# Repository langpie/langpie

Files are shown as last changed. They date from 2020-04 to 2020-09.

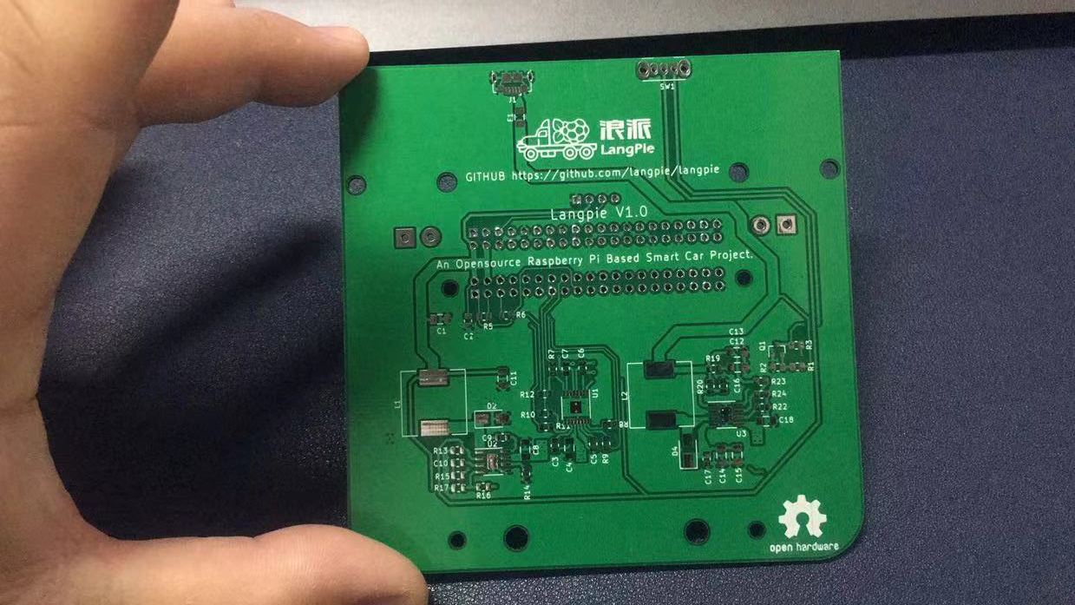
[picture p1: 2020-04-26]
documents/images/real_pcb_v1_0.jpg

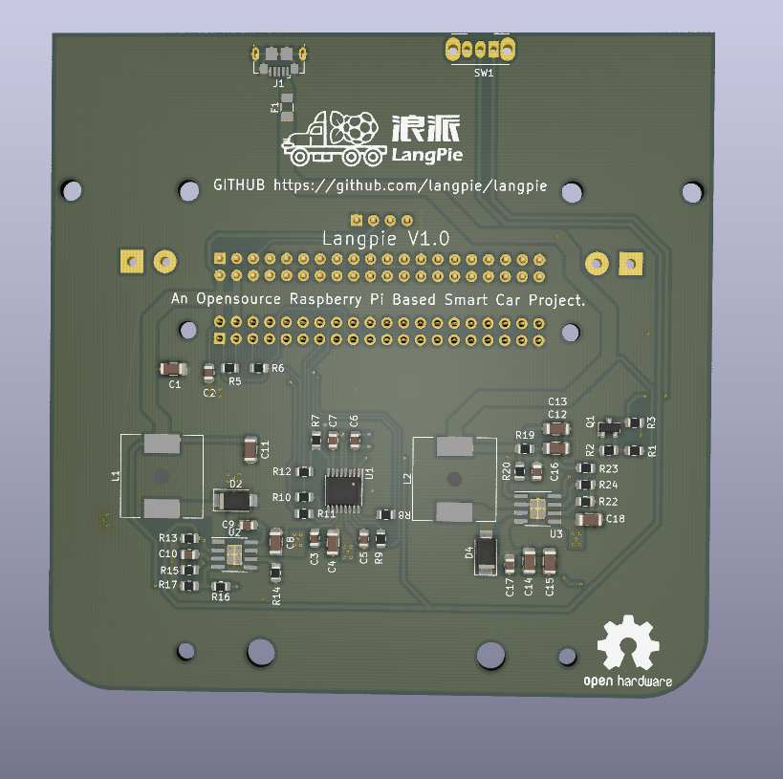
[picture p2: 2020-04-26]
documents/images/pcb_v1_2.png

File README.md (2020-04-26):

# langpie 项目

# 树莓派分布式自动驾驶小车项目-浪派项目
## Respberry Pi LangPie Open Source Project

## 项目目标
* V1.0 阶段: 让树莓派小车能够跑起来(浪)
* V2.0 阶段: 让树莓派能够狠狠的浪(例如加入机器视觉)
* V3.0 阶段: 让树莓派能够狂浪(能够浪到指定地点)
* V4.0 阶段: 让每个人的树莓派能够一起浪(浪派对)
* V5.0 阶段: 让树莓派能够用神经网络自己判断自己该去哪里浪(放浪形骸)
* V6.0 阶段: 树莓派贾维斯浪催的小犊子(没谱)

## 目前状态
### V1.0 版本
- [ ] 电路图绘制
- [ ] 机械图绘制
- [ ] 电路图 Layout
- [ ] 电路板打板
- [ ] 购买元器件
- [ ] 设备焊接
- [ ] 小车组装
- [ ] 树莓派系统安装
- [ ] wiringPi 安装调试
- [ ] 测试电源
- [ ] 测试充电
- [ ] 测试马达
- [ ] 测试树莓派驱动
- [ ] 测试 OLED 屏幕
- [ ] 测试LED 灯
 
## 项目组成员 including Email：

* 圈圈  bg3mdo#langpie.ga
* 漂移菌  yoyojack#langpie.ga
* DoubleDog  doubledog#langpie.ga
* hahaha  hahaha#langpie.ga
* 刘津屹  liujinyi#langpie.ga
* 中华绘图铅笔  pencil#langpie.ga
* 飞鸿  bg3nit#langpie.ga
* 洋洋大叔  bi3qdn#langpie.ga
* 祁建鑫  qjx#langpie.ga
* wjcwqc  wjcwqc#langpie.ga
* 小白 dmuxiaobai#langpie.ga
* lqh  lqh#langpie.ga
* kwanghue kwanghue#langpie.ga
* 张翼 zy#langpie.ga
* iChizer0 

##  项目站点 Project website: 

www.langpie.ga

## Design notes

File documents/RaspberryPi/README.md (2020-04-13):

# Raspberry Pi 树莓派软件准备

## 操作系统镜像

* 强烈推荐: raspbian 
```bash
Distributor ID:	Raspbian
Description:	Raspbian GNU/Linux 10 (buster)
Release:	10
Codename:	buster
```
* 镜像连接: www.raspberrypi.org/downloads/

## 烧录工具

* Etcher: etcher.io
* Win32_diskimager: 请自行百度

## 远程登录工具

* Putty
* Xshell
* SecureCRT
* Rshell
* Powershell

## 文件传输工具

* Windows: 推荐 filezilla / sftp 
* Mac: scp
* Linux: scp

## 自动更换源脚本使用方法
```bash
git clone https://github.com/langpie/langpie.git
cd langpie/documents/RaspberryPi/
chmod +x auto_tsinghua_source.sh
./auto_tsinghua_source.sh
```
### Have Fun

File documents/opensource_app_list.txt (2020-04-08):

# Raspberry Pi Based Open Source Smart Car
# Open Source Design Software

## PCB Design Kit
    -KiCAD
    https://www.kicad-pcb.org/

## Mechanical Design Kit
    -FreeCAD
    https://www.freecadweb.org/

## Image Editor
    -GIMP
    https://www.gimp.org/

## Vector Graphic Editor
    -InkScape
    https://inkscape.org/

## Visio Alternatives
    -Pencil Project
    https://pencil.evolus.vn/

## Office Alternatives
    -LibreOffice
    https://www.libreoffice.org/
    -OpenOffice
    https://www.openoffice.org/
    -WPS
    https://www.wps.com/

## Mind Map
    -XMind
    https://www.xmind.net/

## Project Management
    -GanttProject
    https://www.ganttproject.biz/

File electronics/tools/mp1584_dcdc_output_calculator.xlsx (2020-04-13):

Output(V) | R1(Kilo Ohm) | R2 (Kilo Ohm, Less than 40K) | FB(V)
5.212121212 | 182 | 33 | 0.8
Note that it is better to use E3/E6/E12/E24/E96 standard resistor values

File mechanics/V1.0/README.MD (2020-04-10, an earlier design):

2020.4.10 优化了电机座 完善了摄像头支架 创建了3D打印所需的STL文件

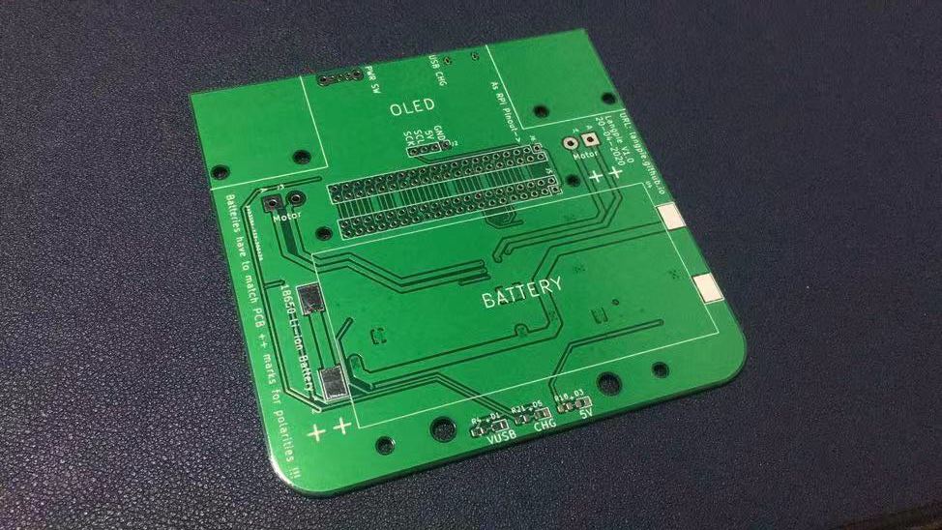
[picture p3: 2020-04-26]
documents/images/real_pcb_v1_1.jpg.jpg

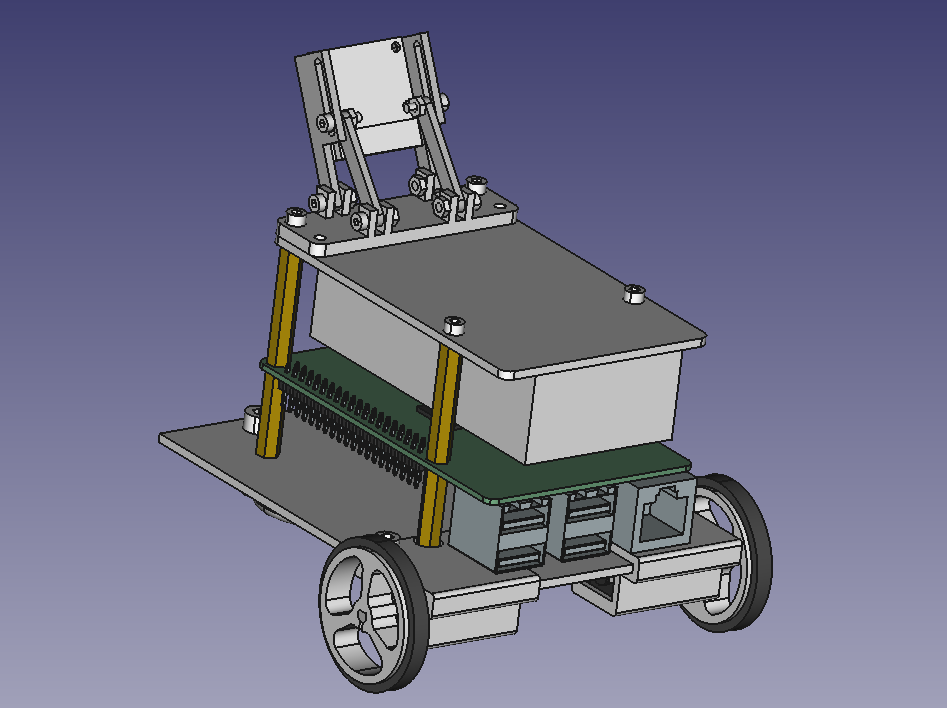
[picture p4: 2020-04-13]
documents/images/cad_v1_1.png

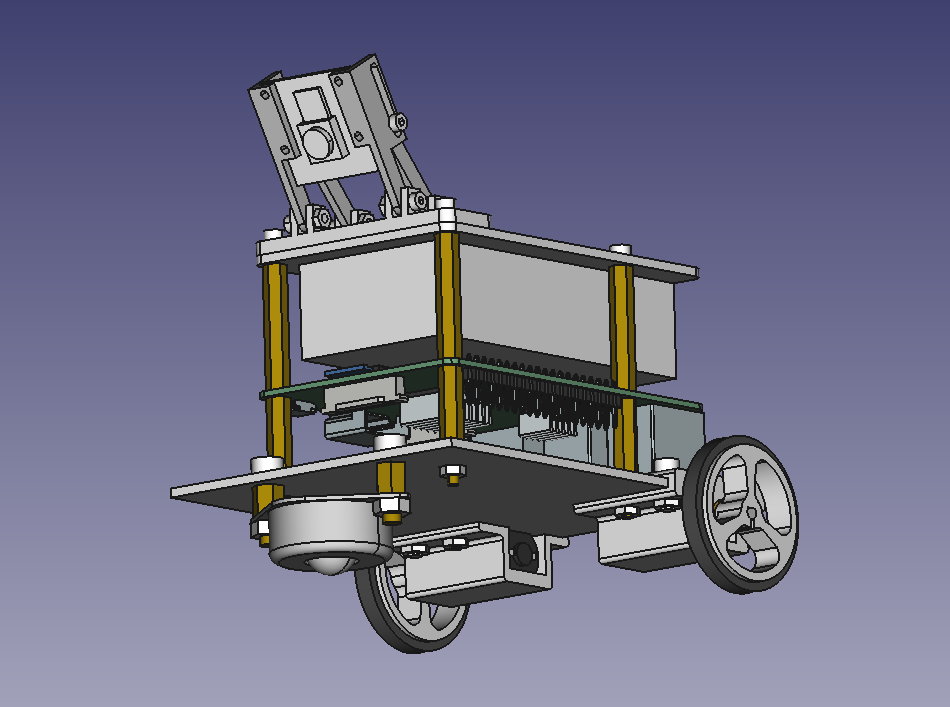
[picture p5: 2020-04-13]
documents/images/cad_v1_0.png

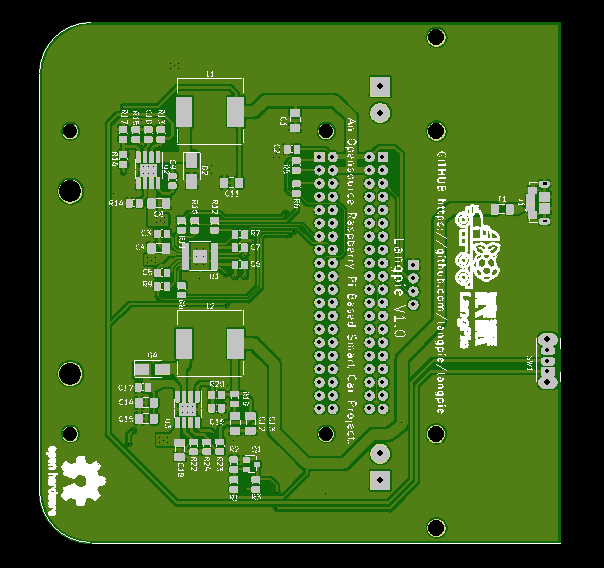
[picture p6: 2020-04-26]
documents/images/fab_v1_preview_0.png

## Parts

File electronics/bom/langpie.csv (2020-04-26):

Id | Designator | Package | Quantity | Designation | Supplier and ref
1 | G*** | logo | 1 | LOGO
2 | REF** | OSHW-Logo2_14.6x12mm_SilkScreen | 1 | OSHW-Logo2_14.6x12mm_SilkScreen
3 | ,,,,, |  | 6
4 | C5 | C_0805_2012Metric | 1 | 2.2uF
5 | R15,R14,R24 | R_0805_2012Metric | 3 | 100K
6 | J6 | PinHeader_2x20_P2.54mm_Vertical | 1 | Conn_02x20_Odd_Even
7 | , , , | MountingHole_2.7mm_M2.5 | 4 | MountingHole_2.7mm_M2.5
8 | , | MountingHole_4.3mm_M4 | 2 | MountingHole_4.3mm_M4
9 | , , , | MountingHole_3.2mm_M3 | 4 | MountingHole_3.2mm_M3
10 | C1 | C_1206_3216Metric | 1 | 10nF
11 | C2,C6,C7,C9 | C_0805_2012Metric | 4 | 100nF
12 | C3 | C_0805_2012Metric | 1 | 10nF
13 | C4,C8,C12,C18 | C_1206_3216Metric | 4 | 10uF
14 | C10 | C_0805_2012Metric | 1 | 150pF
15 | C11,C13,C14,C15 | C_1206_3216Metric | 4 | 22uF
16 | C16,C17 | C_0805_2012Metric | 2 | 1uF
17 | D1,D3,D5 | LED_0805_2012Metric | 3 | LED
18 | D2,D4 | D_SMA | 2 | B340A-13-F
19 | F1 | Fuse_1206_3216Metric | 1 | Fuse
20 | J1 | USB_Micro-B_GCT_USB3076-30-A | 1 | USB_B_Micro
21 | J2 | PinHeader_1x04_P2.54mm_Vertical | 1 | Conn_01x04
22 | J3,J4 | SolderWirePad_1x02_P5.08mm_Drill1.5mm | 2 | Conn_01x02
23 | J5 | PinSocket_2x20_P2.54mm_Vertical | 1 | Conn_02x20_Odd_Even
24 | L1 | L_12x12mm_H6mm | 1 | 15uH
25 | L2 | L_12x12mm_H6mm | 1 | 2.2uH
26 | Q1 | SOT-23 | 1 | 2N7000
27 | R1,R4,R18 | R_0805_2012Metric | 3 | 1K
28 | R2,R13 | R_0805_2012Metric | 2 | 47K
29 | R3,R5,R6,R12 | R_0805_2012Metric | 4 | 10K
30 | R7,R8,R9,R10,R11,R21 | R_0805_2012Metric | 6 | 200R
31 | R16 | R_0805_2012Metric | 1 | 182K
32 | R17 | R_0805_2012Metric | 1 | 33K
33 | R19,R20 | R_0805_2012Metric | 2 | 2R
34 | R22 | R_0805_2012Metric | 1 | 6.8K
35 | R23 | R_0805_2012Metric | 1 | 270K
36 | SW1 | SW_CuK_OS102011MA1QN1_SPDT_Angled | 1 | SW_SPDT
37 | U1 | HTSSOP-16-1EP_4.4x5mm_P0.65mm_EP3.4x5mm_Mask2.46x2.31mm_ThermalVias | 1 | DRV8833PWP
38 | U3 | SOIC-8-1EP_3.9x4.9mm_P1.27mm_EP2.29x3mm_ThermalVias | 1 | CS5080E
39 | U4 | li-battery-case | 1 | 18650-Battery
40 | U2 | SOIC-8-1EP_3.9x4.9mm_P1.27mm_EP2.29x3mm_ThermalVias | 1 | MP1584

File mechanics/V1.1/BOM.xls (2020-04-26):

项目号 | 零件号 | 说明 | 数量 | 型号 | 淘宝链接
1 | N20 wheel |  | 2
2 | M2.5 28+6 |  | 6
3 | M2.5 nut |  | 4
4 | M3 8 hexagon socket head cap screw |  | 4
5 | M3 nut |  | 4
6 | N20 motor |  | 2
7 | M4 6 hexagon socket head cap screw |  | 2
8 | ball wheel |  | 1 | 12A | https://detail.tmall.com/item.htm?spm=a230r.1.14.28.3d3b42fdA0ATDi&id=590284019863&ns=1&abbucket=13
9 | M4 7+6 copper cylinder |  | 2
10 | M4 nut |  | 2
11 | battery holder |  | 1
12 | M2 6 hexagon socket head cap screw |  | 2
13 | M2 nut |  | 6
14 | M2 8 hexagon socket head cap screw |  | 4

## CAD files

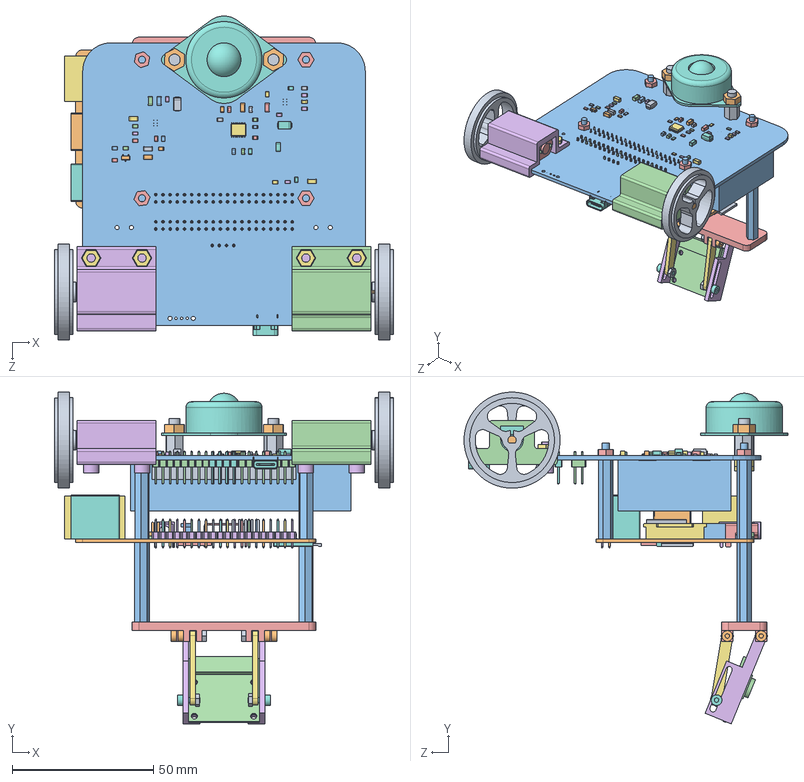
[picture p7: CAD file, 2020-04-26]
mechanics/V1.1/car.SLDASM
120.0 x 117.4 x 114.6 mm
N20 wheel x 2
Raspberry Pi 3_1.stp
Raspberry Pi 3_1_1.stp
Raspberry Pi 3_2.stp
Raspberry Pi 3_3.stp
Raspberry Pi 3_4.stp
Raspberry Pi 3_5.stp
Raspberry Pi 3_6.stp
Raspberry Pi 3_7.stp
Raspberry Pi 3_8.stp
Raspberry Pi 3_9.stp
Raspberry Pi 3_10.stp
Raspberry Pi 3_11.stp
Raspberry Pi 3_12.stp
Raspberry Pi 3_13.stp
Raspberry Pi 3_14.stp
Raspberry Pi 3_15.stp
Raspberry Pi 3_16.stp
Raspberry Pi 3_17.stp
Raspberry Pi 3_18.stp
Raspberry Pi 3_19.stp
Raspberry Pi 3_20.stp
Raspberry Pi 3_21.stp
Raspberry Pi 3_22.stp
Raspberry Pi 3_23.stp
Raspberry Pi 3_24.stp
Raspberry Pi 3_25.stp
Raspberry Pi 3_26.stp
Raspberry Pi 3_27.stp
Raspberry Pi 3_28.stp
Raspberry Pi 3_29.stp
Raspberry Pi 3_30.stp
Raspberry Pi 3_31.stp
Raspberry Pi 3_32.stp
Raspberry Pi 3_33.stp
Raspberry Pi 3_34.stp
Raspberry Pi 3_35.stp
Raspberry Pi 3_36.stp
Raspberry Pi 3_37.stp
Raspberry Pi 3_38.stp
Raspberry Pi 3_39.stp
Raspberry Pi 3_40.stp
Raspberry Pi 3_41.stp
Raspberry Pi 3_42.stp
Raspberry Pi 3_43.stp
Raspberry Pi 3_44.stp
Raspberry Pi 3_45.stp
Raspberry Pi 3_46.stp
Raspberry Pi 3 (micro SD).stp
Raspberry Pi 3_47.stp
Raspberry Pi 3_48.stp
Raspberry Pi 3_49.stp
Raspberry Pi 3_50.stp
Raspberry Pi 3_51.stp
Raspberry Pi 3_52.stp
Raspberry Pi 3_53.stp
RPi Heatsink Set.stp
RPi Heatsink Set_1.stp
M2.5 28+6 x 6
N20 lift mounting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

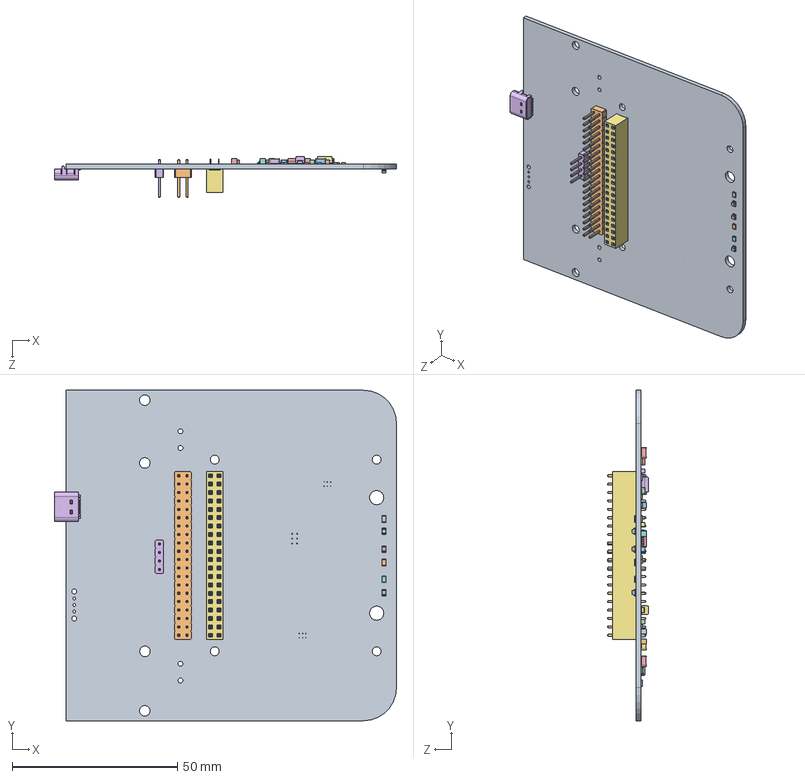
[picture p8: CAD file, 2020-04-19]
mechanics/V1.1/CAR PCB/car pcb.SLDASM
103.5 x 100.0 x 12.4 mm
J6_PinHeader_2x20_P254mm_Vertical_5E973953
D1_LED_0805_2012Metric_5E97381B
D3_LED_0805_2012Metric_5E973846
D5_LED_0805_2012Metric_5E973871
J2_PinHeader_1x04_P254mm_Vertical_5E9738C1
J5_PinSocket_2x20_P254mm_Vertical_5E975A58
R4_R_0805_2012Metric_5E99E94D
R18_R_0805_2012Metric_5E9C048F
R21_R_0805_2012Metric_5E973B6B
C5_C_0805_2012Metric_5E97372B
R15_R_0805_2012Metric_5E973B05
C1_C_1206_3216Metric_5E9736E7
C2_C_0805_2012Metric_5E9736F8
C3_C_0805_2012Metric_5E973709
C4_C_1206_3216Metric_5E97BBAC
C6_C_0805_2012Metric_5E97B6B1
C7_C_0805_2012Metric_5E97374D
C8_C_1206_3216Metric_5E97375E
C9_C_0805_2012Metric_5E97376F
C10_C_0805_2012Metric_5E973780
C11_C_1206_3216Metric_5E973791
C12_C_1206_3216Metric_5E977737
C13_C_1206_3216Metric_5E978263
C14_C_1206_3216Metric_5E9737C4
C15_C_1206_3216Metric_5E9737D5
C16_C_0805_2012Metric_5E9737E6
C17_C_0805_2012Metric_5E9737F7
C18_C_1206_3216Metric_5E973808
D2_D_SMA_5E9BCED4
D4_D_SMA_5E9777E8
Q1_SOT_23_5E99EF72
R1_R_0805_2012Metric_5E973A17
R2_R_0805_2012Metric_5E973A28
R3_R_0805_2012Metric_5E973A39
R5_R_0805_2012Metric_5E973A5B
R6_R_0805_2012Metric_5E973A6C
R7_R_0805_2012Metric_5E973A7D
R8_R_0805_2012Metric_5E973A8E
R9_R_0805_2012Metric_5E97BAD9
R10_R_0805_2012Metric_5E973AB0
R11_R_0805_2012Metric_5E973AC1
R12_R_0805_2012Metric_5E97B756
R13_R_0805_2012Metric_5E973AE3
R14_R_0805_2012Metric_5E973AF4
R16_R_0805_2012Metric_5E973B16
R17_R_0805_2012Metric_5E973B27
R19_R_0805_2012Metric_5E973B49
R20_R_0805_2012Metric_5E973B5A
R22_R_0805_2012Metric_5E973B7C
R23_R_0805_2012Metric_5E9785CC
R24_R_0805_2012Metric_5E973B9E
U1_TSSOP_16_1EP_44x5mm_Pitch065mm_EP34x5mm_5E973BE1
User Library-USB Type C Port (SMD Type)

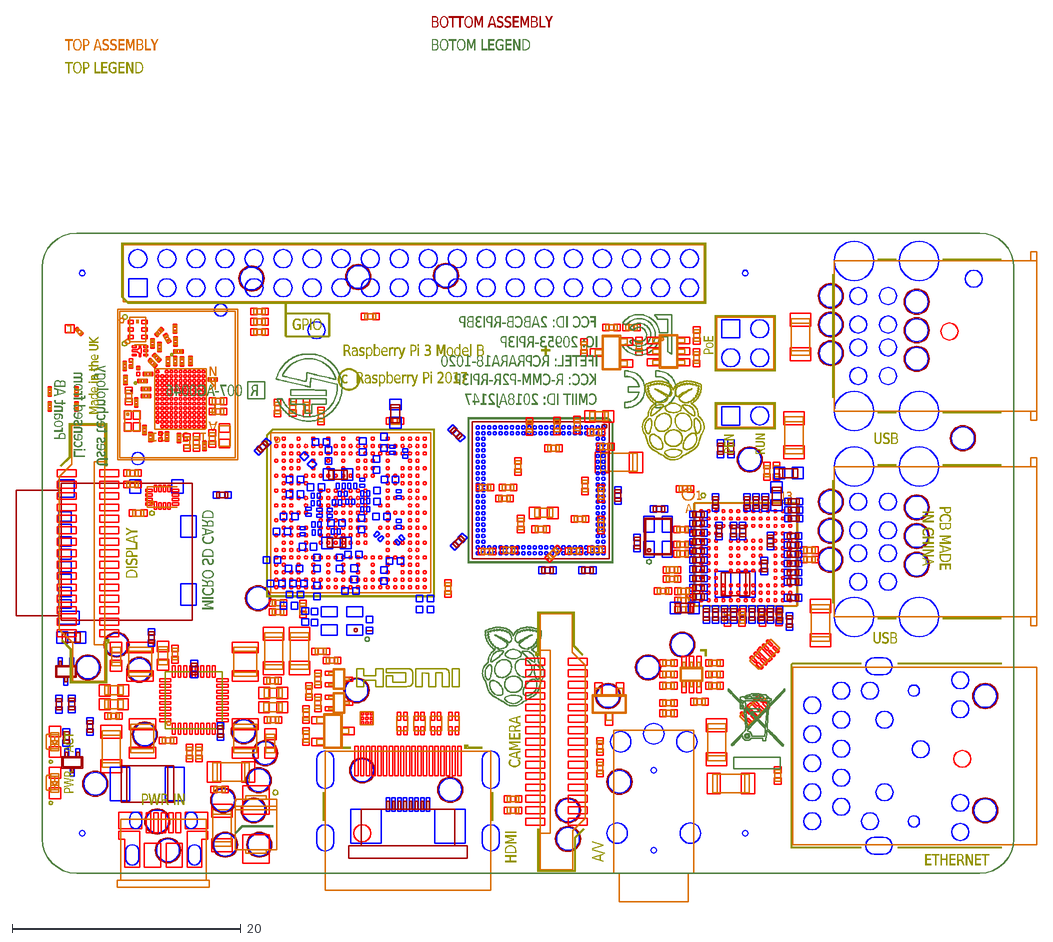
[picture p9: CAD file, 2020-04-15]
electronics/dxf/rpi_MECH_3bplus.dxf
11
5
1
N
K
E
A
13
R 007-AG0046
CMIIT ID: 2018AJ2147
KCC: R-CMM-P2R-RPI3P
IFETEL: RCPRARA18-1020
IN CHINA
PCB MADE
PEN
IC: 20953-RPI3P
FCC ID: 2ABCB-RPI3BP
Licensed from
Proant AB
Uses technology
PoE
c Raspberry Pi 2017
Raspberry Pi 3 Model B
MICRO SD CARD
HDMI
BOTOM LEGEND
BOTTOM ASSEMBLY
TOP LEGEND
TOP ASSEMBLY
Made in the UK
A/V
GPIO
USB
ETHERNET
PWR IN
DISPLAY
CAMERA
RUN
ACT
PWR

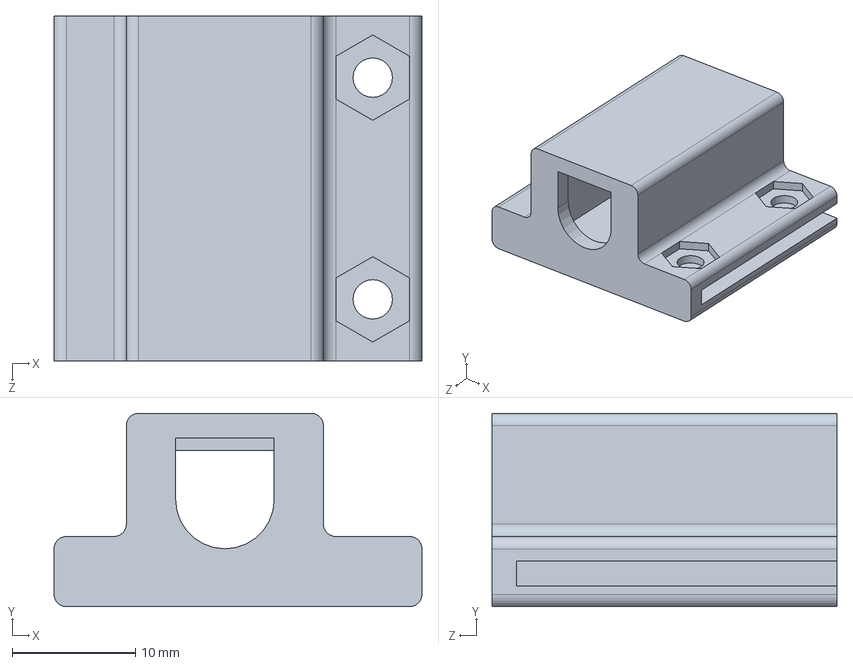
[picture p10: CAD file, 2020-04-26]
mechanics/V1.1/N20 lift mounting.sldprt
29.9 x 15.7 x 28.0 mm

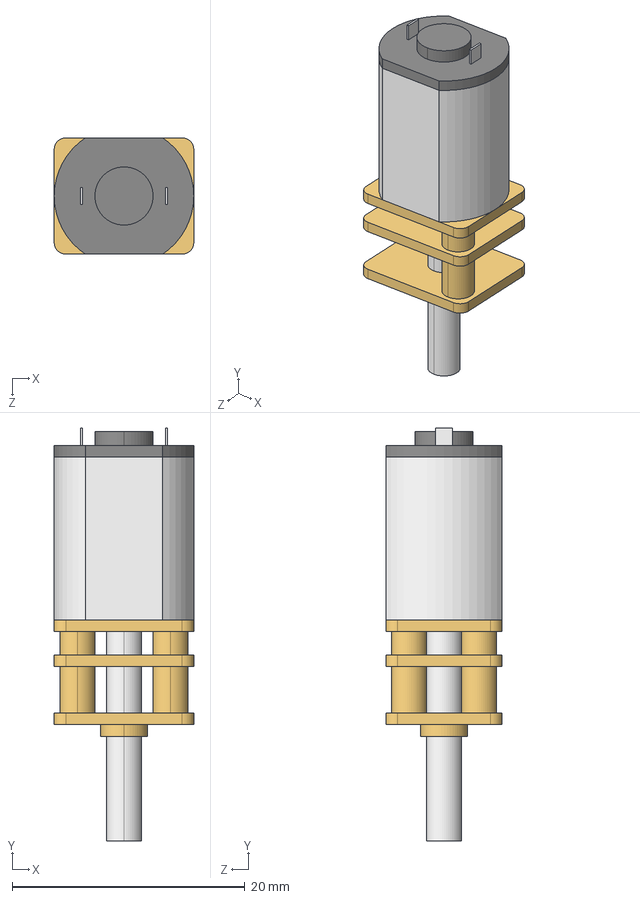
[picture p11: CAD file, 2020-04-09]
mechanics/V1.1/N20motor/User Library-N20.STEP
12.0 x 35.5 x 10.0 mm
User Library-N20_Pad010
User Library-N20_Pad009
User Library-N20_Pad008
User Library-N20_Pad006
User Library-N20_Pad004
User Library-N20_Pad003

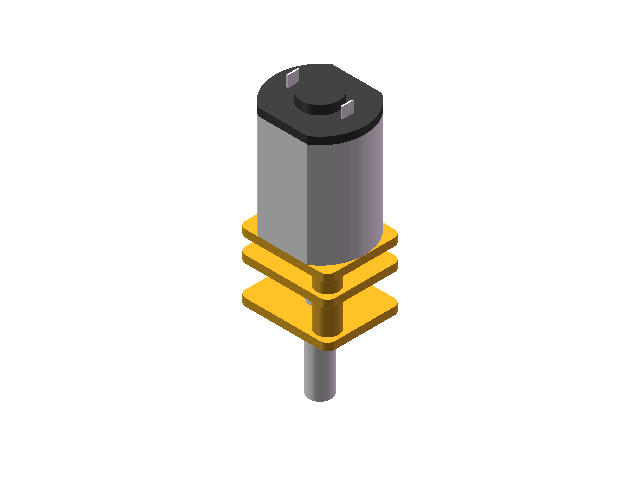
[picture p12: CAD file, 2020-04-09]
mechanics/V1.1/N20motor/N20 motor.SLDASM
User Library-N20_Pad010^User Library-N20(2)
User Library-N20_Pad009^User Library-N20(2)
User Library-N20_Pad008
User Library-N20_Pad006^User Library-N20(2)
User Library-N20_Pad004^User Library-N20(2)
User Library-N20_Pad003^User Library-N20(2)

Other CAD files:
mechanics/V1.1/N20motor/User Library-N20(2).sldasm
mechanics/V1.1/12864oled/Pins.sldasm
mechanics/V1.1/CAR PCB/Top.sldasm
mechanics/V1.1/12864oled/PinHeader.sldasm
mechanics/V1.1/Raspberry/Raspberry Pi 3.stp.SLDASM
mechanics/V1.1/CAR PCB/Step_Models.sldasm
mechanics/V1.1/CAR PCB/Board_Geoms.sldasm
mechanics/V1.1/CAR PCB/Bot.sldasm
mechanics/V1.1/CAR PCB/Pcb.sldasm
mechanics/V1.1/12864oled/128x64Oled v3.sldprt
mechanics/V1.1/CAR PCB/D2_D_SMA_5E9BCED4.sldprt
mechanics/V1.1/Raspberry/Raspberry Pi 3_4.stp.SLDPRT
mechanics/V1.0/DXF/battery pcb.DXF
mechanics/V1.0/DXF/car baseplate.DXF
mechanics/V1.0/M2 nut.SLDPRT
mechanics/V1.0/M2.5 20+6.SLDPRT
mechanics/V1.0/M2.5 28+6.SLDPRT
mechanics/V1.0/M2.5 8 hexagon socket head cap screw.SLDPRT
mechanics/V1.0/M2.5 nut.SLDPRT
mechanics/V1.0/M3 8 hexagon socket head cap screw.SLDPRT
mechanics/V1.0/M3 nut.SLDPRT
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

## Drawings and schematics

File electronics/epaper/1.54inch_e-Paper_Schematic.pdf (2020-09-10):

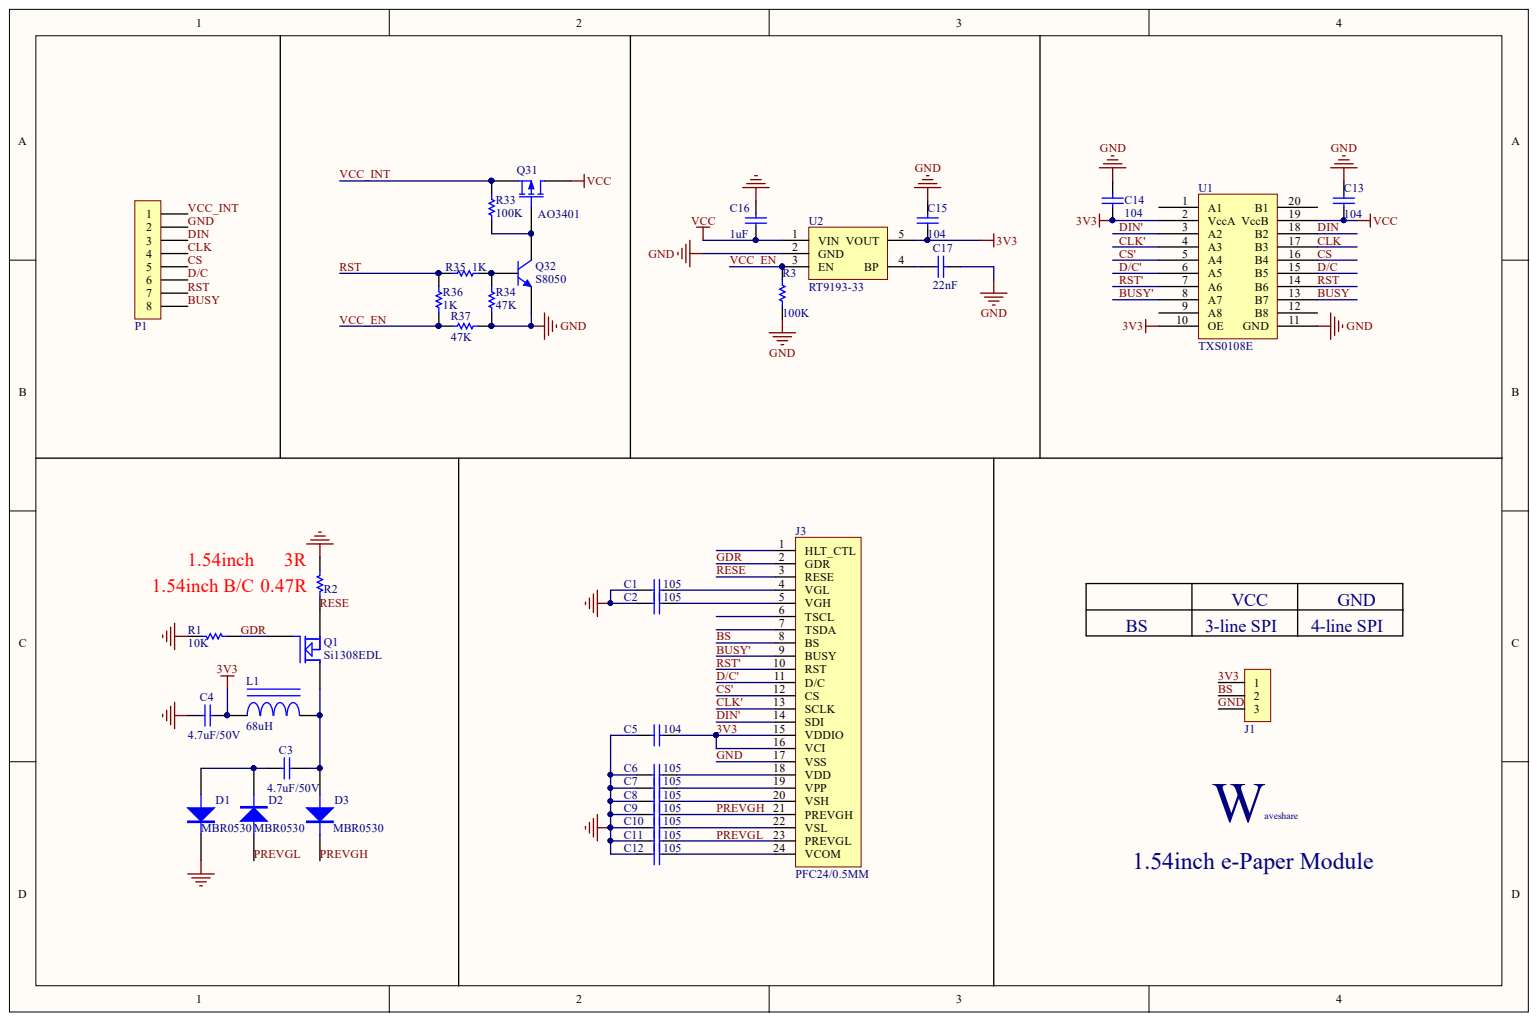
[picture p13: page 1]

VCC | GND

BS | 3-line SPI | 4-line SPI

C7 | 105
C8 | 105
C9 | 105 PREVGH
C10 | 105
C11 | 105 PREVGL
C12 | 105

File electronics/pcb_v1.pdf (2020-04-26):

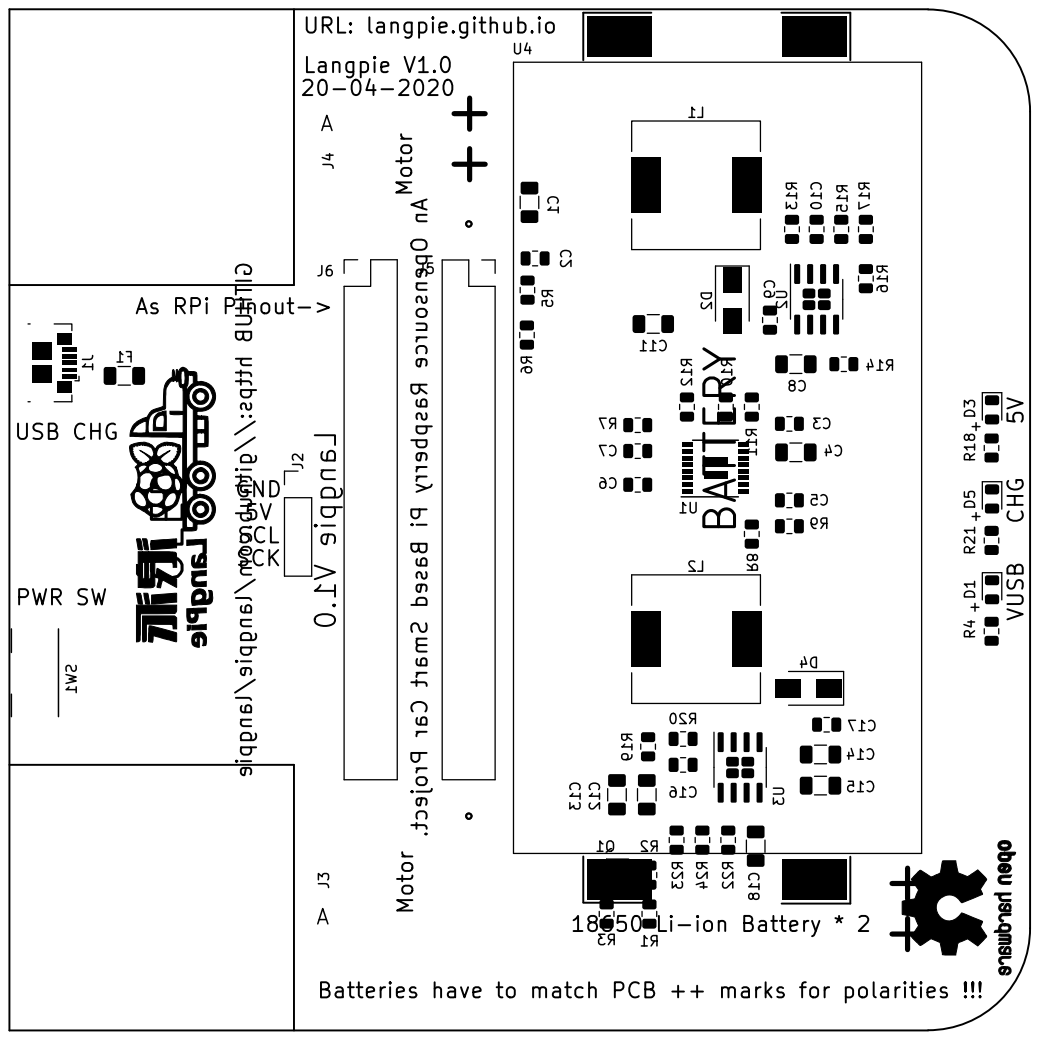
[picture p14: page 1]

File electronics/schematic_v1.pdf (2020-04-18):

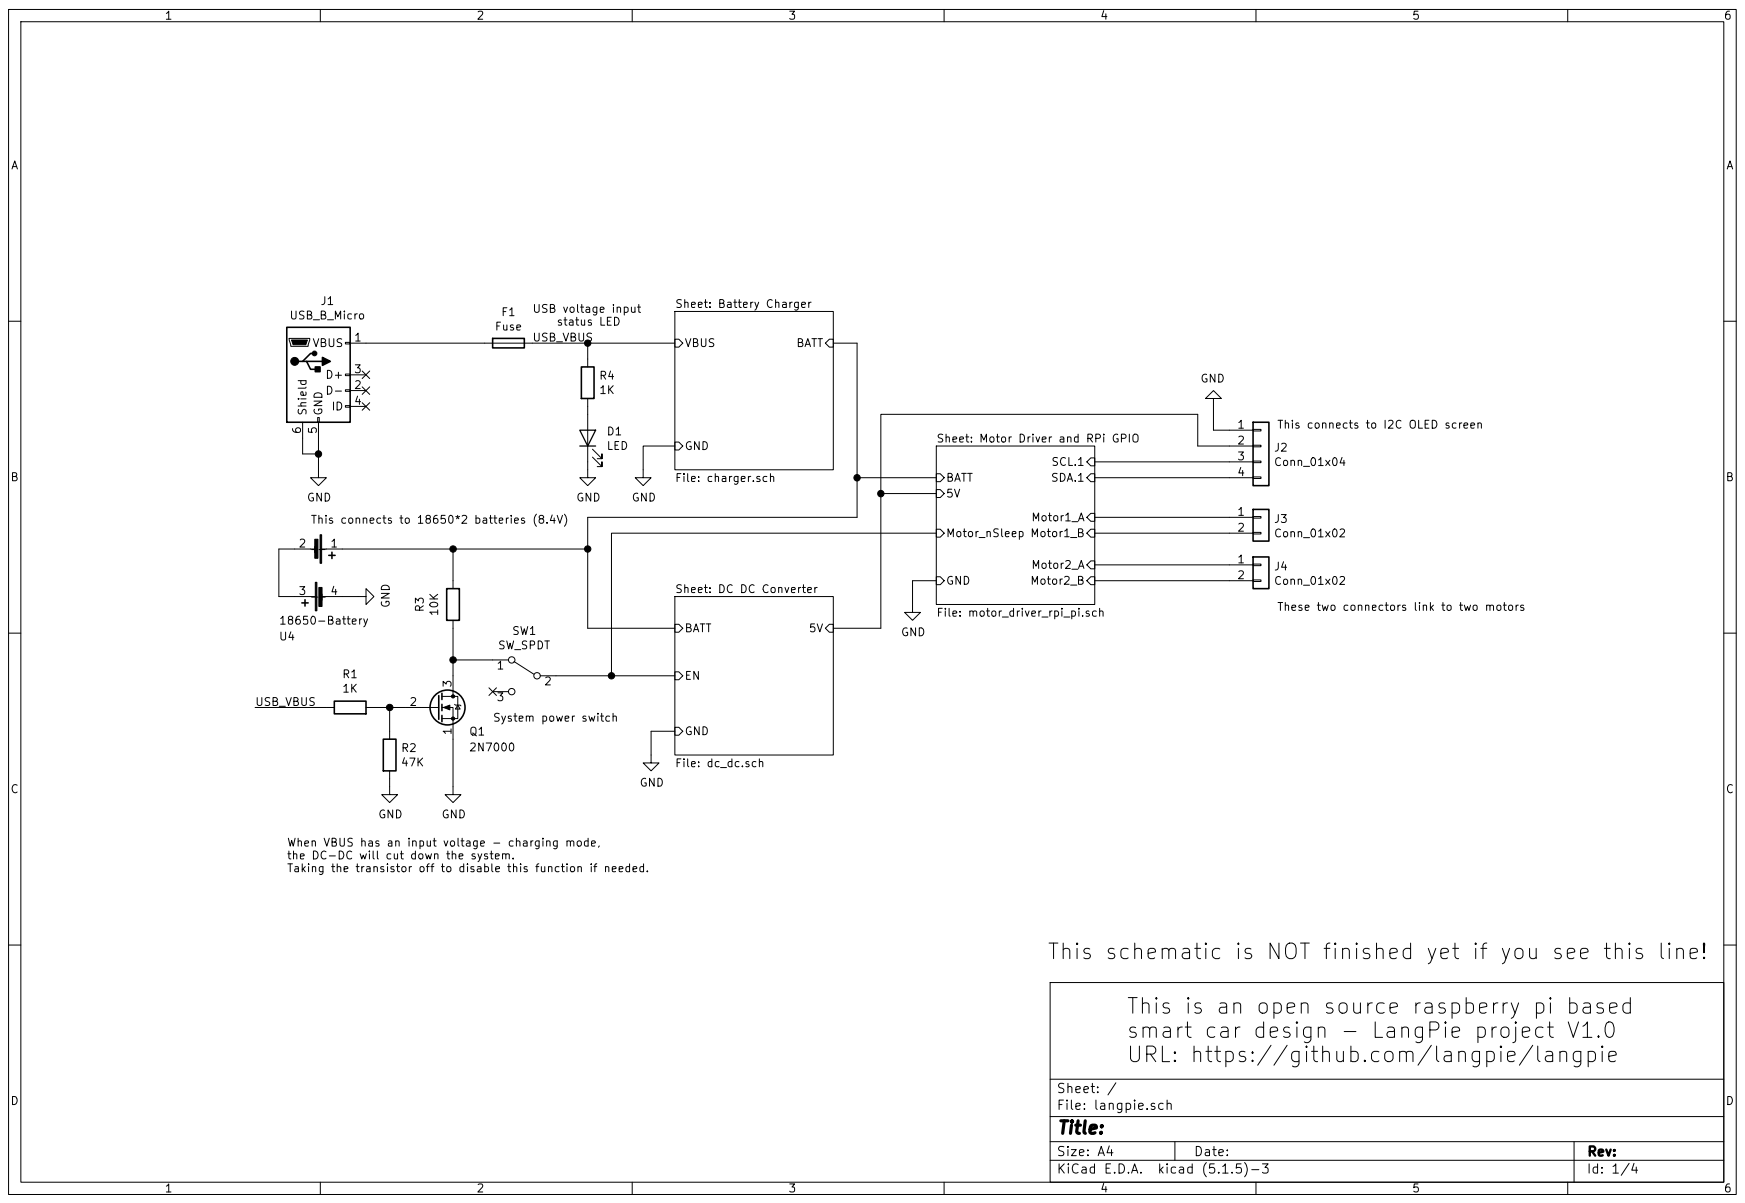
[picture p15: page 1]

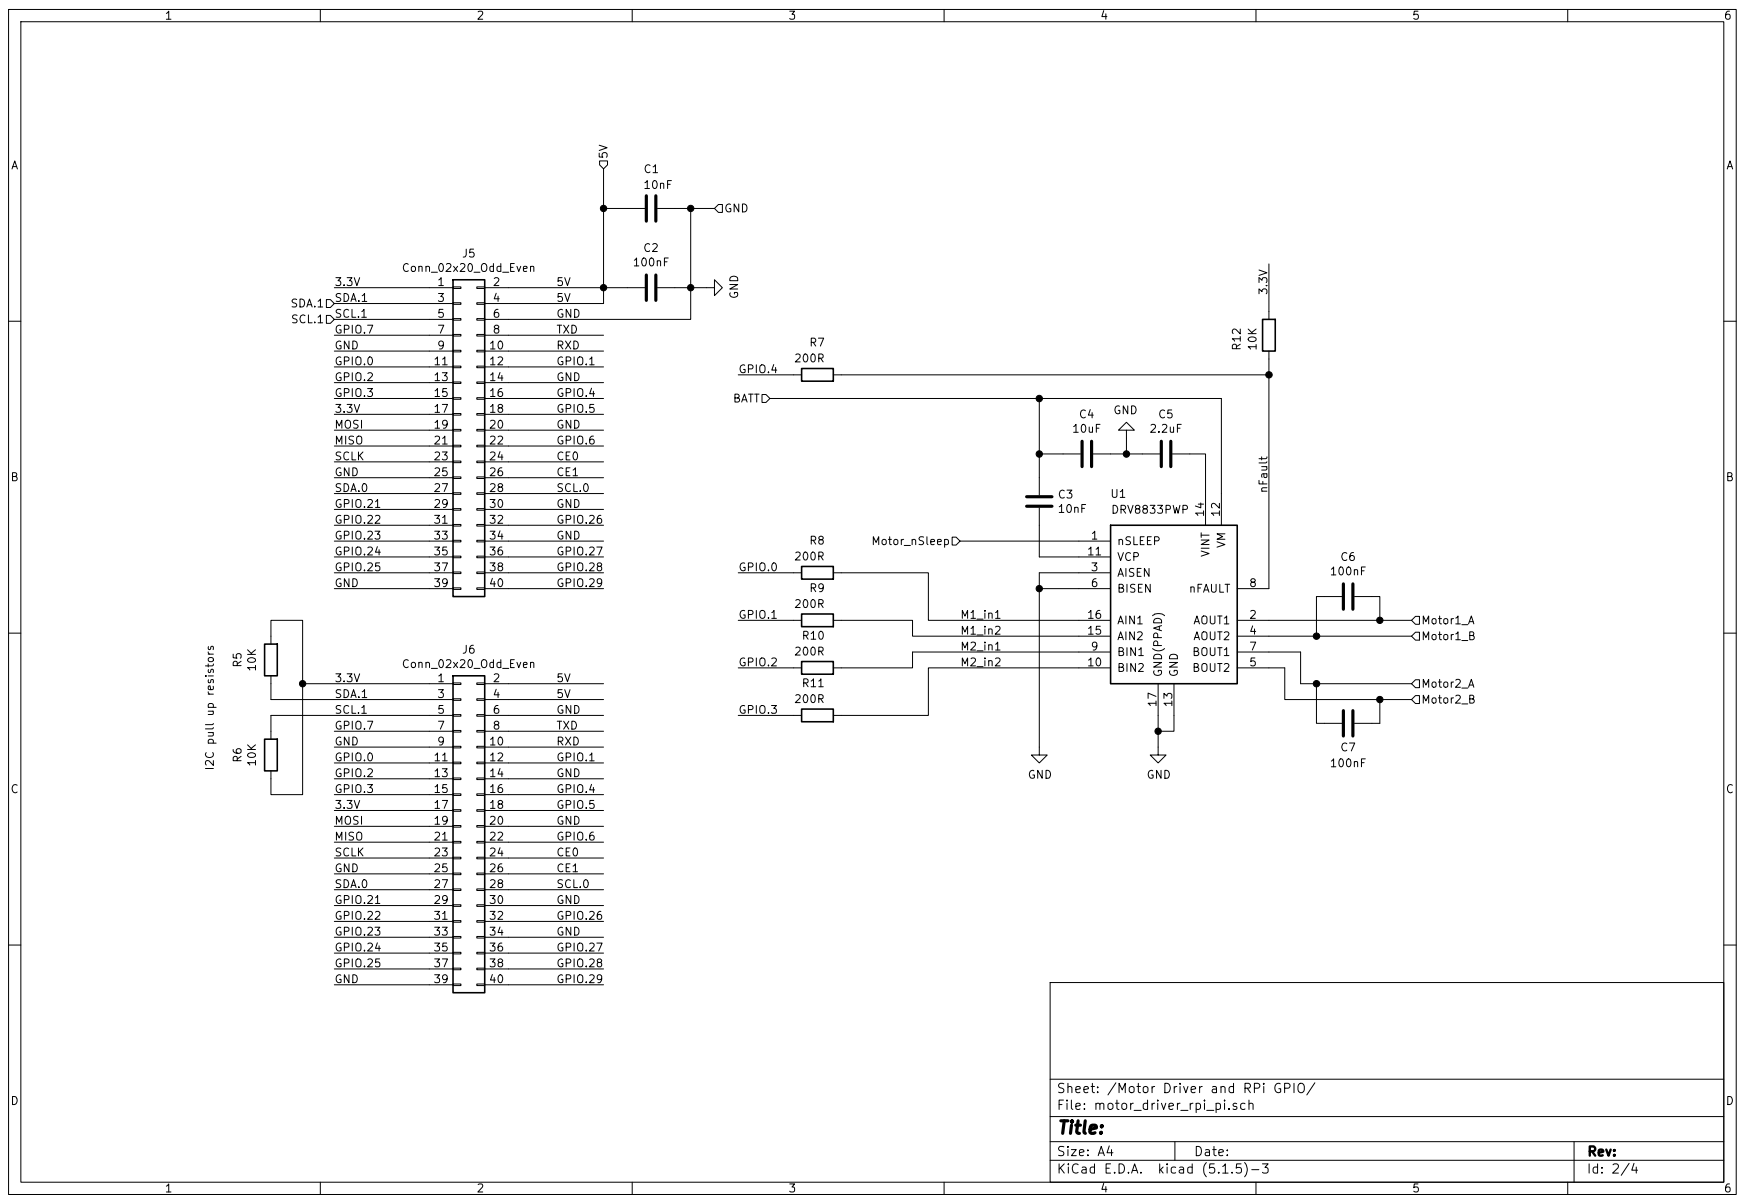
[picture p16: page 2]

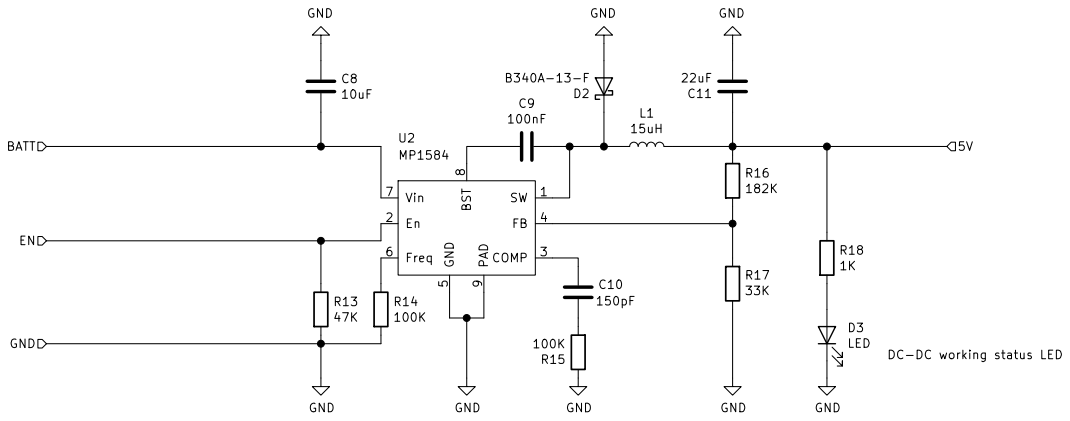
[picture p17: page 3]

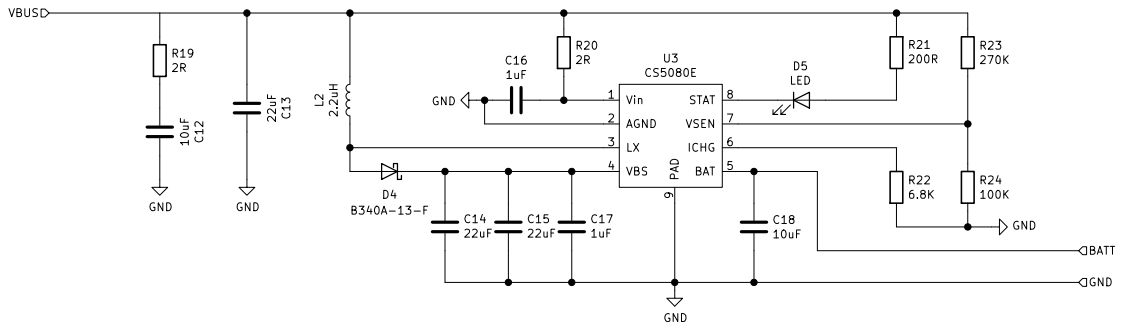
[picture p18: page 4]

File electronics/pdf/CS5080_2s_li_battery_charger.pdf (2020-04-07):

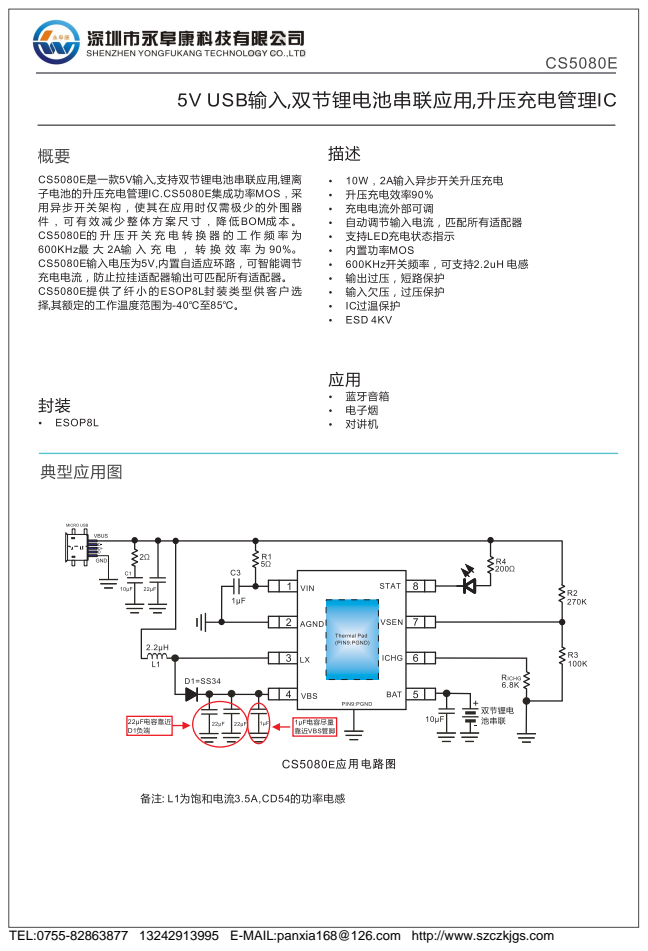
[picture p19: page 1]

TEL:0755-82863877 13242913995 E-MAIL:panxia168@126.com http://www.szczkjgs.com

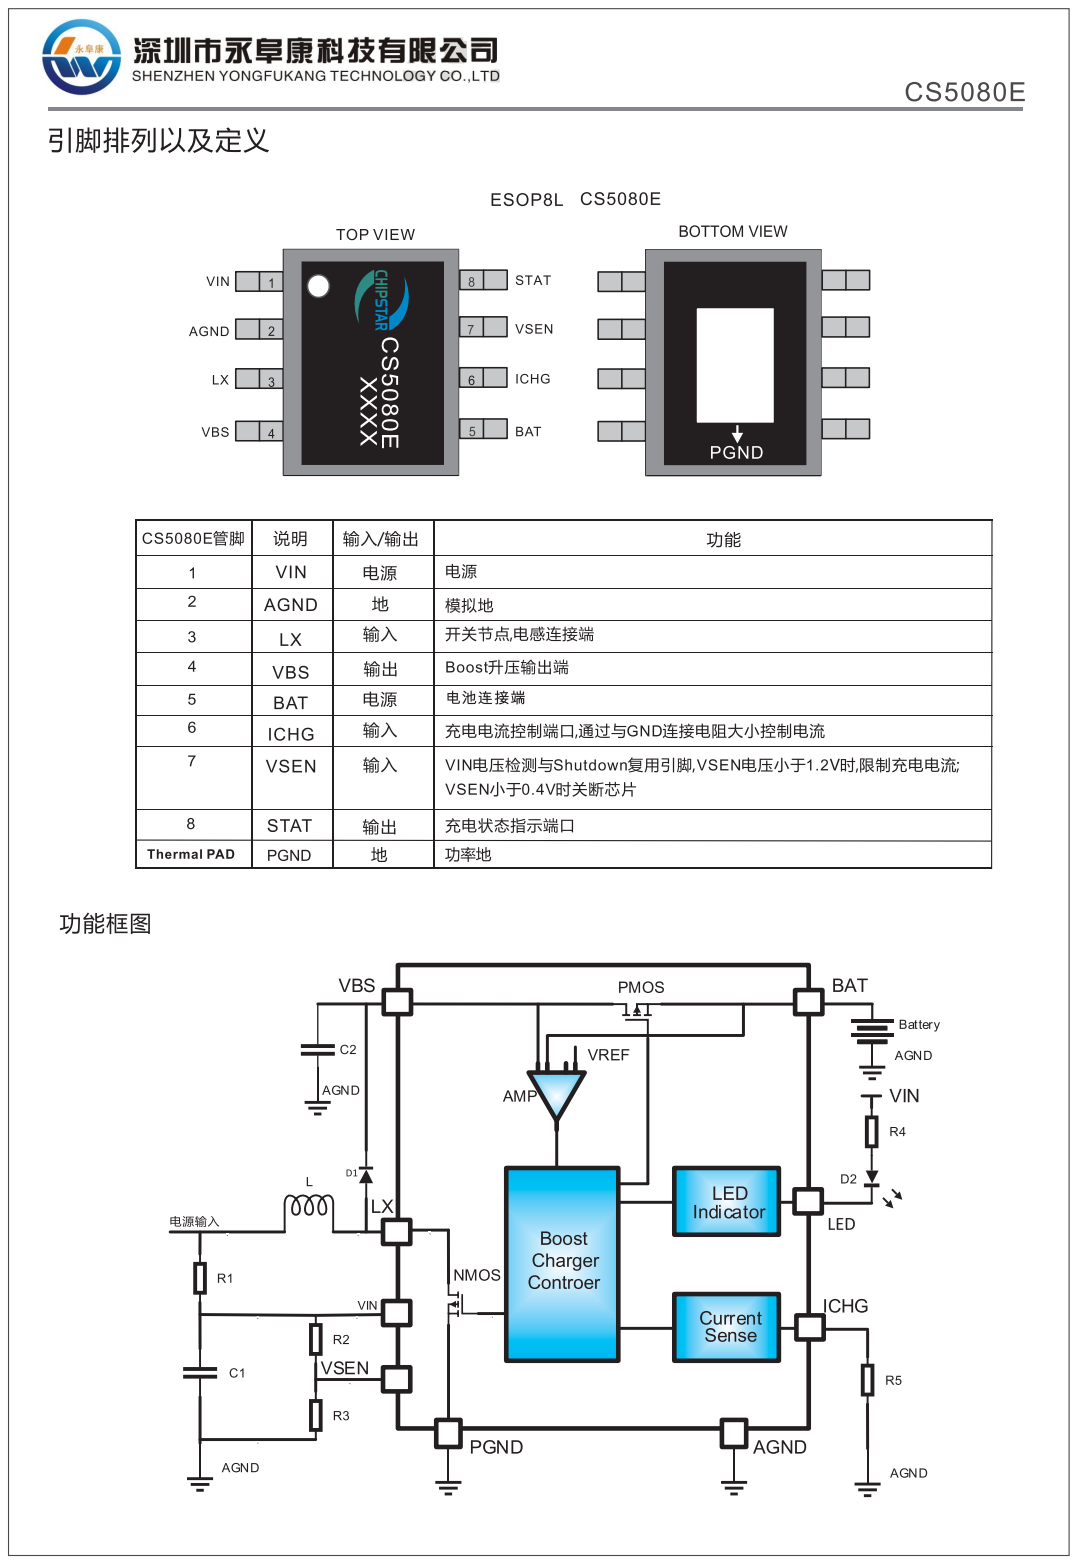
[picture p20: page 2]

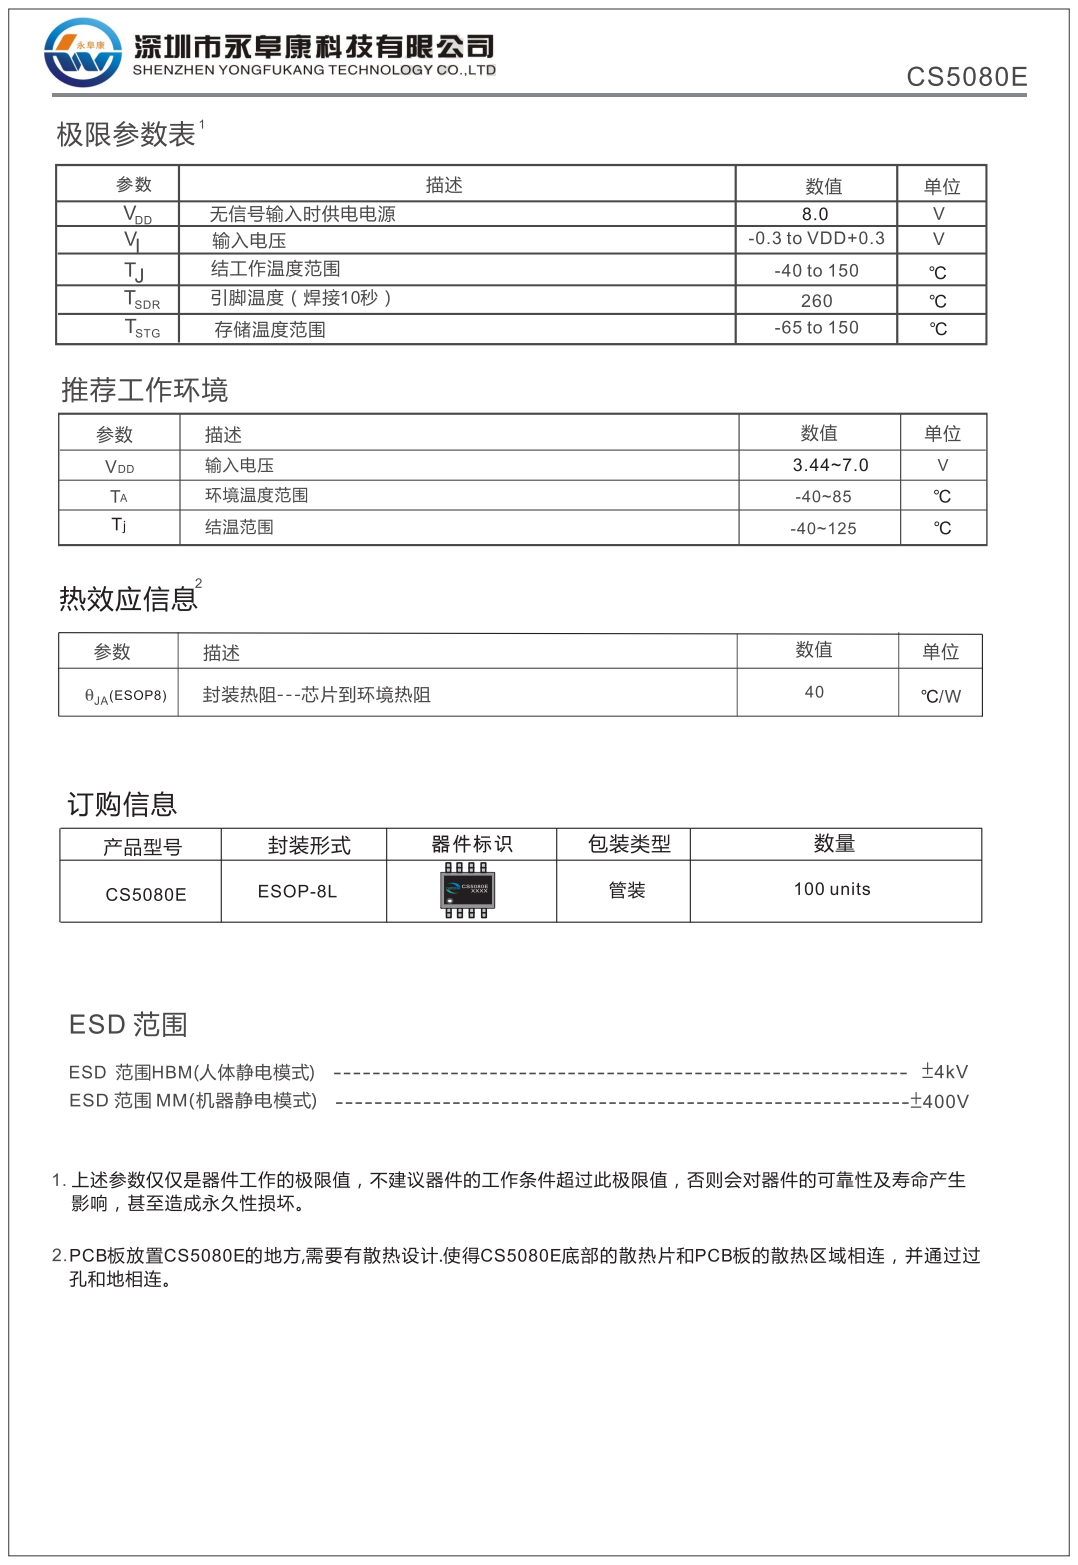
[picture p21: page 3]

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

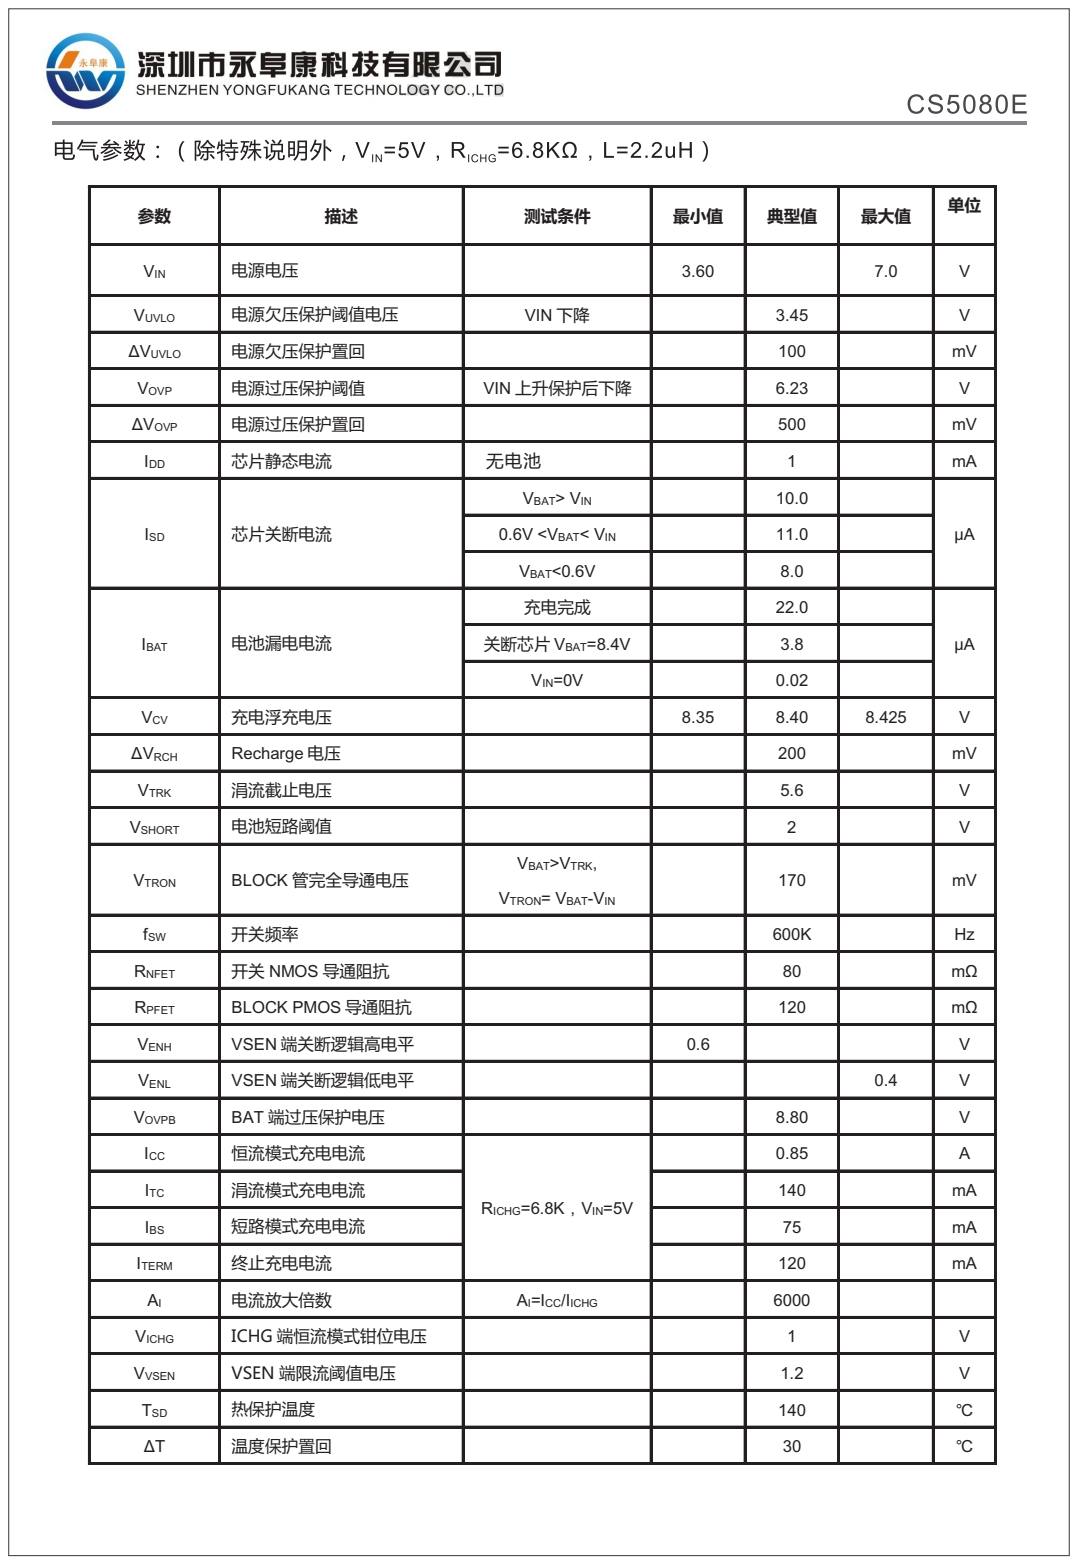
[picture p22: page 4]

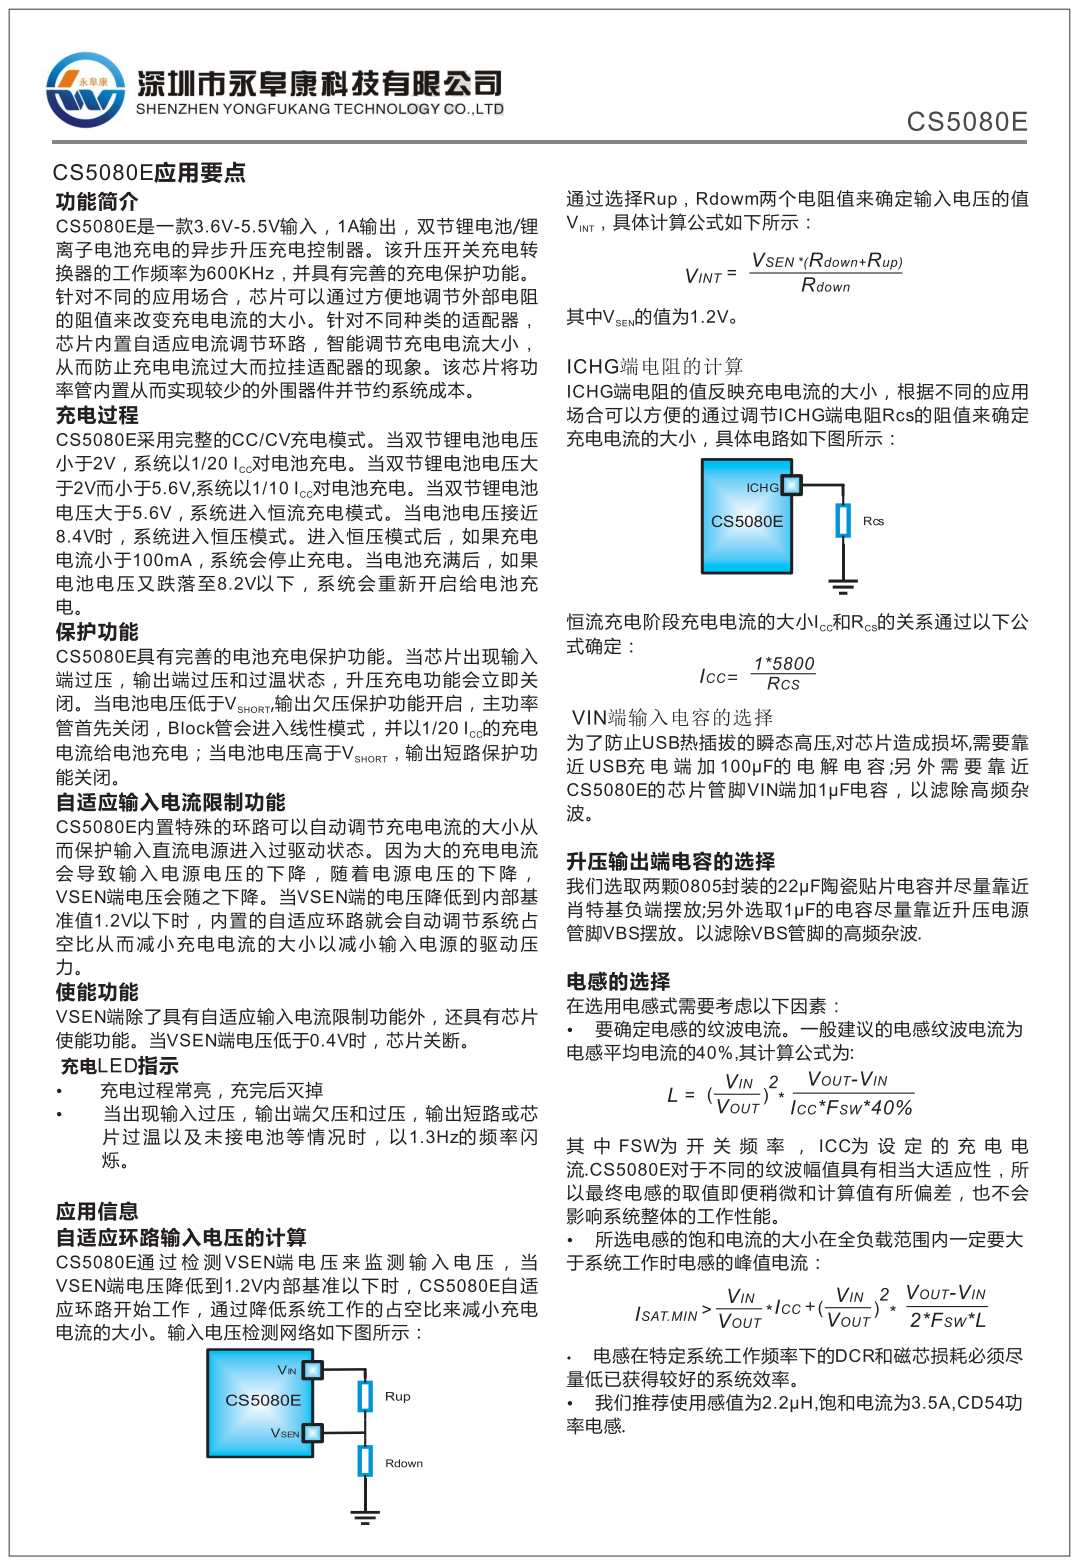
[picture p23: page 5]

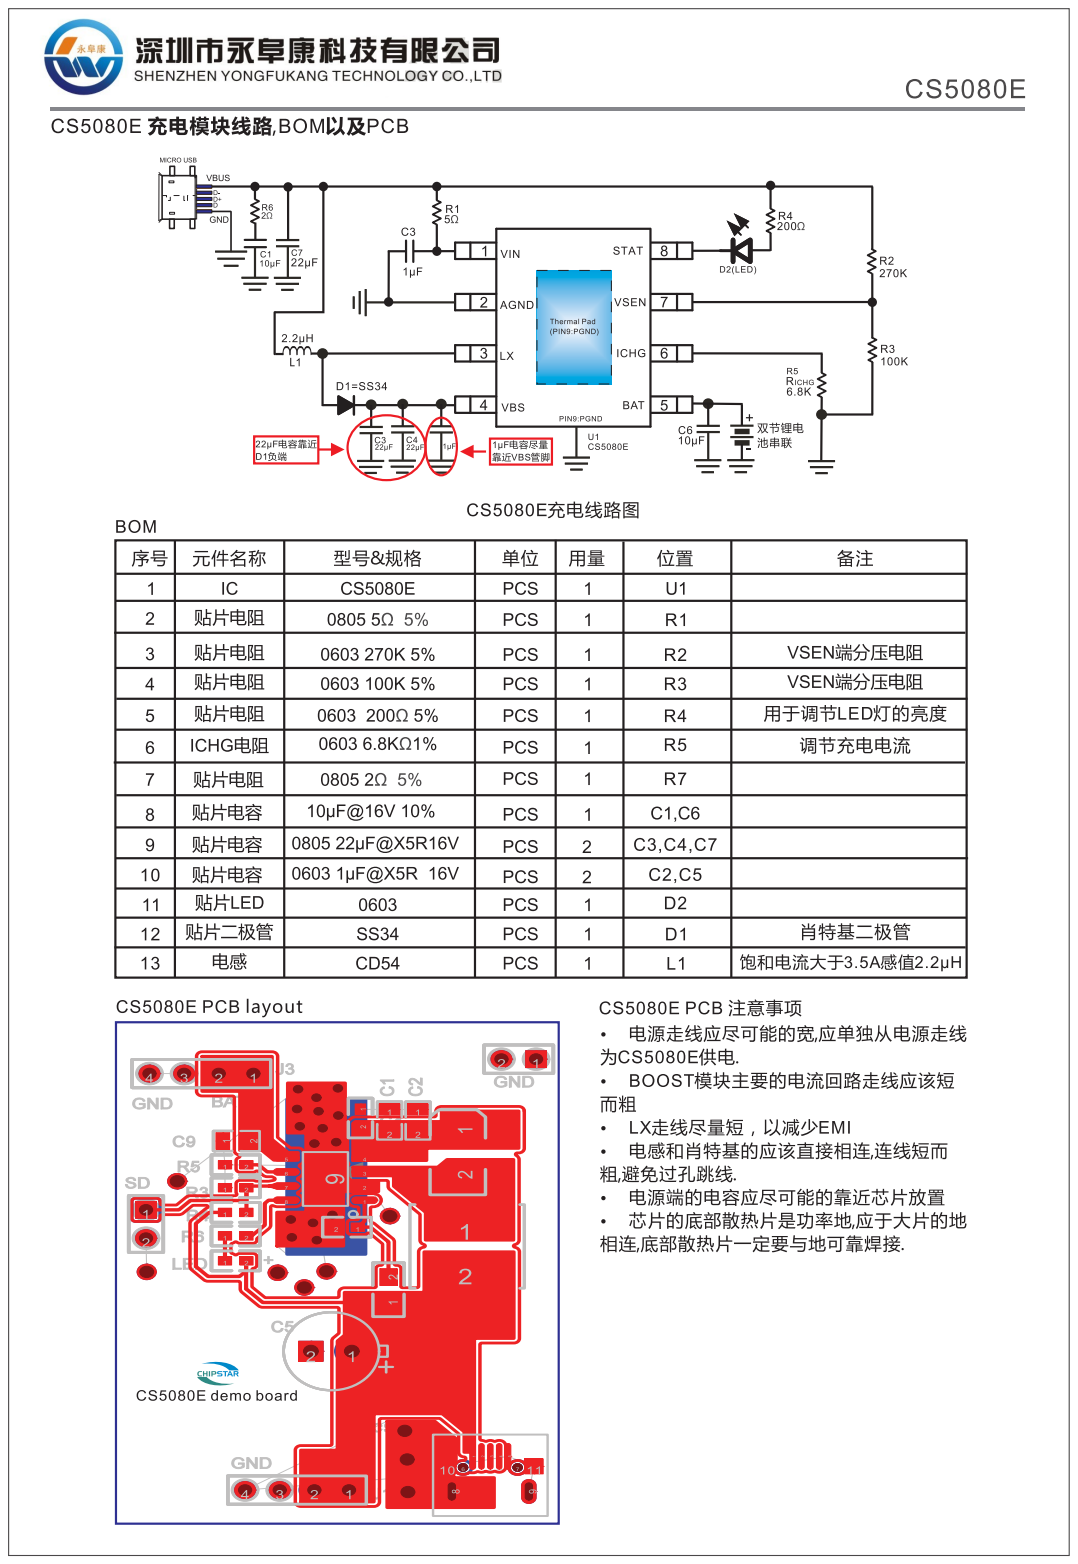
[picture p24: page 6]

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

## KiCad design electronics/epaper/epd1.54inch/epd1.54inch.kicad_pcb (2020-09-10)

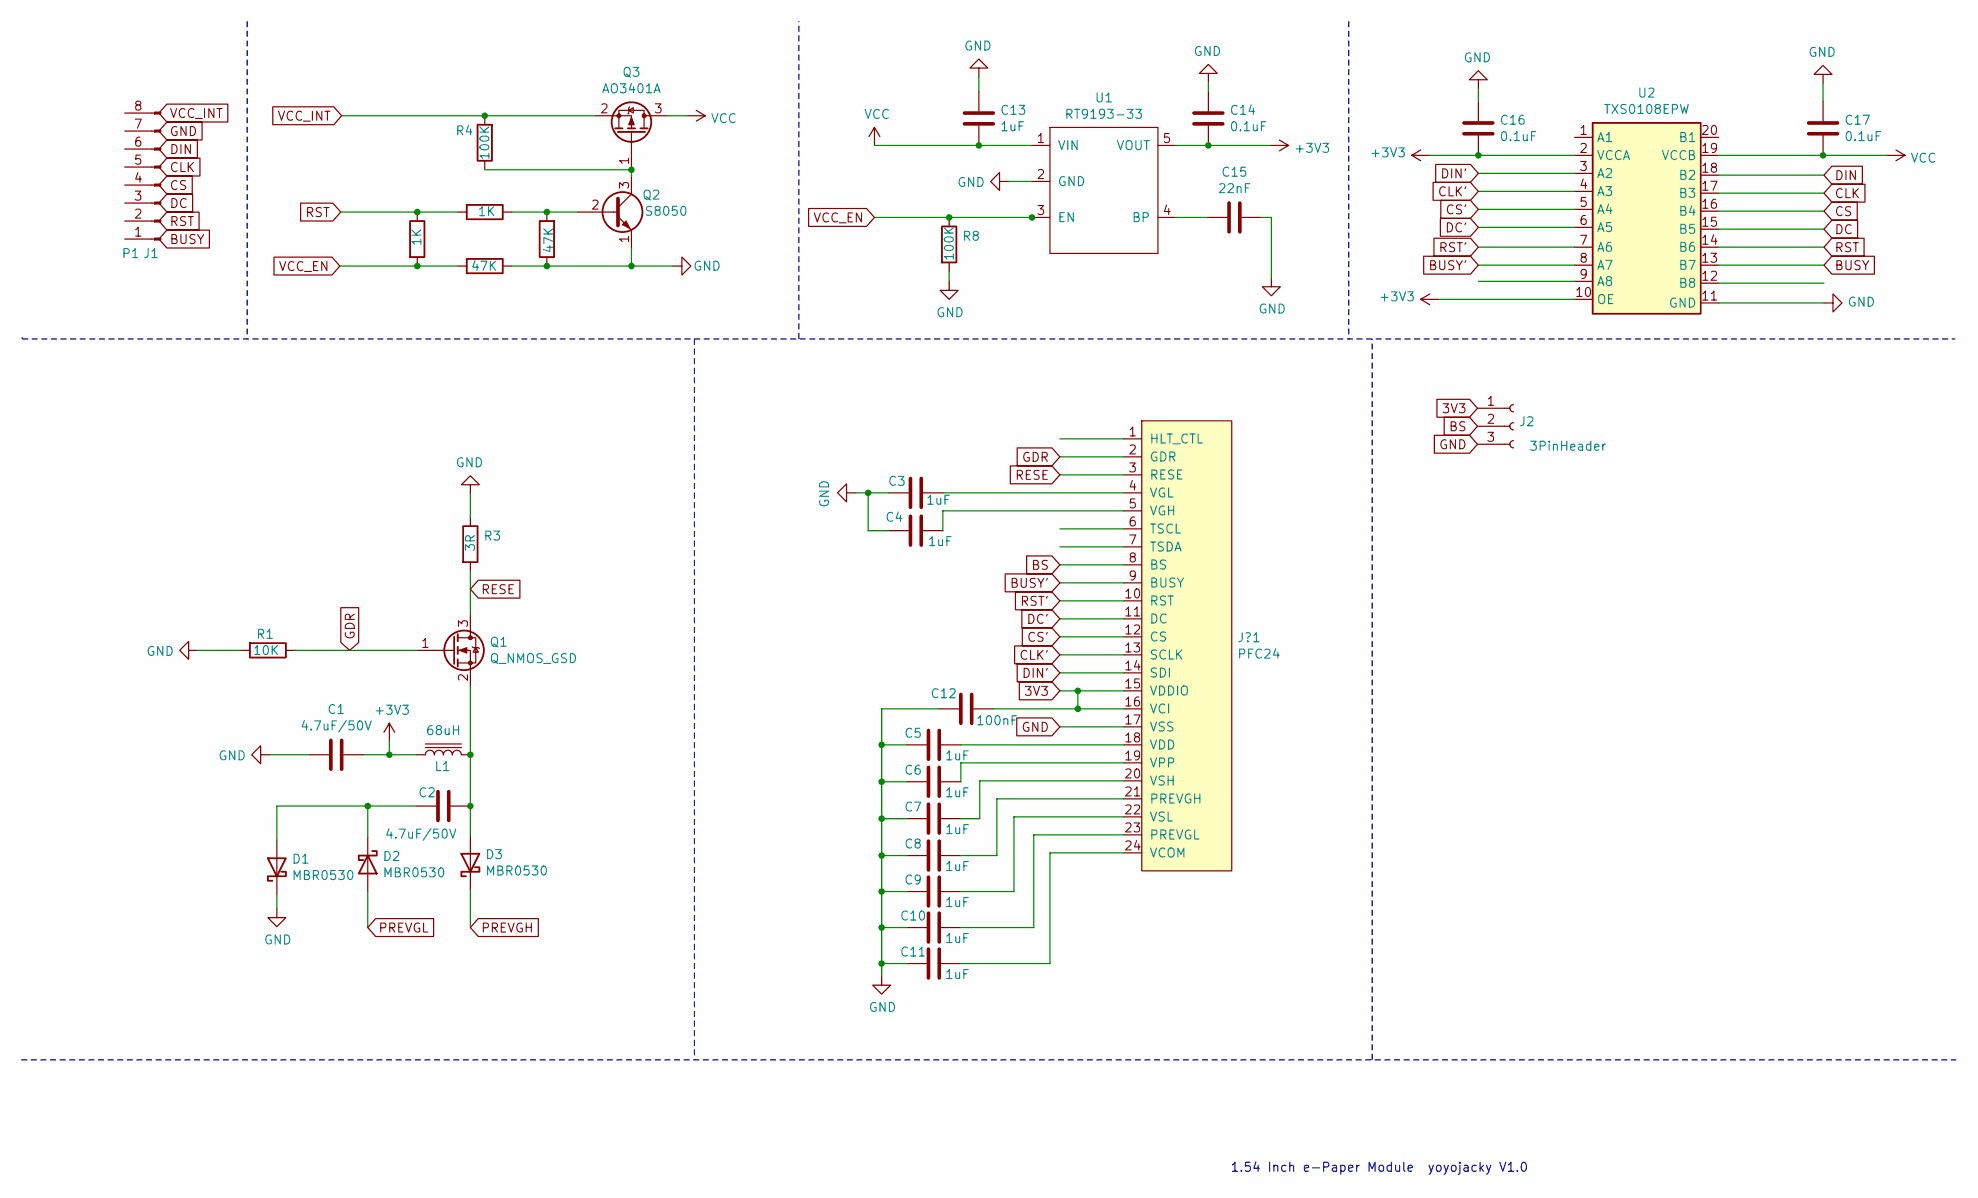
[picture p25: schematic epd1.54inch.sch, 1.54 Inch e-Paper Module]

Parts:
C1, C2: 4.7uF/50V; C_0603_1608Metric_Pad1.05x0.95mm_HandSolder
C3, C4, C5, C6, C7, C8, C9, C10, C11, C13: 1uF; C_0603_1608Metric_Pad1.05x0.95mm_HandSolder
C12: 100nF; C_0603_1608Metric_Pad1.05x0.95mm_HandSolder
C14, C16, C17: 0.1uF; C_0603_1608Metric_Pad1.05x0.95mm_HandSolder
C15: 22nF; C_0603_1608Metric_Pad1.05x0.95mm_HandSolder
D1, D2, D3: MBR0530; D_SOD-123
J1: P1; PinHeader_1x08_P2.54mm_Vertical
J2: 3PinHeader; PinHeader_1x03_P2.54mm_Vertical
J?1: PFC24; Hirose_FH12-24S-0.5SH_1x24-1MP_P0.50mm_Horizontal
L1: 68uH; L_10.4x10.4_H4.8
Q1: Q_NMOS_GSD; SOT-323_SC-70_Handsoldering
Q2: S8050; TO-92_Inline
Q3: AO3401A; SOT-23
R1: 10K; R_0603_1608Metric_Pad1.05x0.95mm_HandSolder
R2, R5: 1K; R_0603_1608Metric_Pad1.05x0.95mm_HandSolder
R3: 3R; R_0603_1608Metric_Pad1.05x0.95mm_HandSolder
R4, R8: 100K; R_0603_1608Metric_Pad1.05x0.95mm_HandSolder
R6, R7: 47K; R_0603_1608Metric_Pad1.05x0.95mm_HandSolder
U1: RT9193-33; SOT-23-5
U2: TXS0108EPW; TSSOP-20_4.4x6.5mm_P0.65mm

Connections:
3V3: C12.1, J2.1, J?1.15 (VDDIO), J?1.16 (VCI)
+3V3: C1.1, C14.2, C16.2, L1.1, U1.5 (VOUT), U2.2 (VCCA), U2.10 (OE)
BS: J2.2, J?1.8 (BS)
BUSY: U2.13 (B7)
BUSY': J?1.9 (BUSY), U2.8 (A7)
CLK: U2.17 (B3)
CLK': J?1.13 (SCLK), U2.4 (A3)
CS: U2.16 (B4)
CS': J?1.12 (CS), U2.5 (A4)
DC: U2.15 (B5)
DC': J?1.11 (DC), U2.6 (A5)
DIN: U2.18 (B2)
DIN': J?1.14 (SDI), U2.3 (A2)
GDR: J?1.2 (GDR), Q1.1 (G), R1.1
GND: C1.2, C3.2, C4.2, C5.2, C6.2, C7.2, C8.2, C9.2, C10.2, C11.2, C12.2, C13.2, C14.1, C15.1, C16.1, C17.1, D1.1 (K), J2.3, J?1.17 (VSS), Q2.1 (E), R1.2, R3.1, R6.1, R7.1, R8.2, U1.2 (GND), U2.11 (GND)
unnamed: C2.1, D1.2 (A), D2.1 (K)
unnamed: C2.2, D3.2 (A), L1.2, Q1.2 (S)
unnamed: C3.1, J?1.4 (VGL)
unnamed: C4.1, J?1.5 (VGH)
unnamed: C5.1, J?1.18 (VDD)
unnamed: C6.1, J?1.19 (VPP)
unnamed: C7.1, J?1.20 (VSH)
unnamed: C8.1, J?1.21 (PREVGH)
unnamed: C9.1, J?1.22 (VSL)
unnamed: C10.1, J?1.23 (PREVGL)
unnamed: C11.1, J?1.24 (VCOM)
unnamed: C15.2, U1.4 (BP)
unnamed: Q2.2 (B), R5.1, R7.2
unnamed: Q2.3 (C), Q3.1 (G), R4.1
PREVGH: D3.1 (K)
PREVGL: D2.2 (A)
RESE: J?1.3 (RESE), Q1.3 (D), R3.2
RST: R2.1, R5.2, U2.14 (B6)
RST': J?1.10 (RST), U2.7 (A6)
VCC: C13.1, C17.2, Q3.3 (D), U1.1 (VIN), U2.19 (VCCB)
VCC_EN: R2.2, R6.2, R8.1, U1.3 (EN)
VCC_INT: Q3.2 (S), R4.2

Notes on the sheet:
1.54 Inch e-Paper Module yoyojacky V1.0

Board: 2 copper layers, 37 parts (0 on the bottom side), 30 nets, no tracks yet.

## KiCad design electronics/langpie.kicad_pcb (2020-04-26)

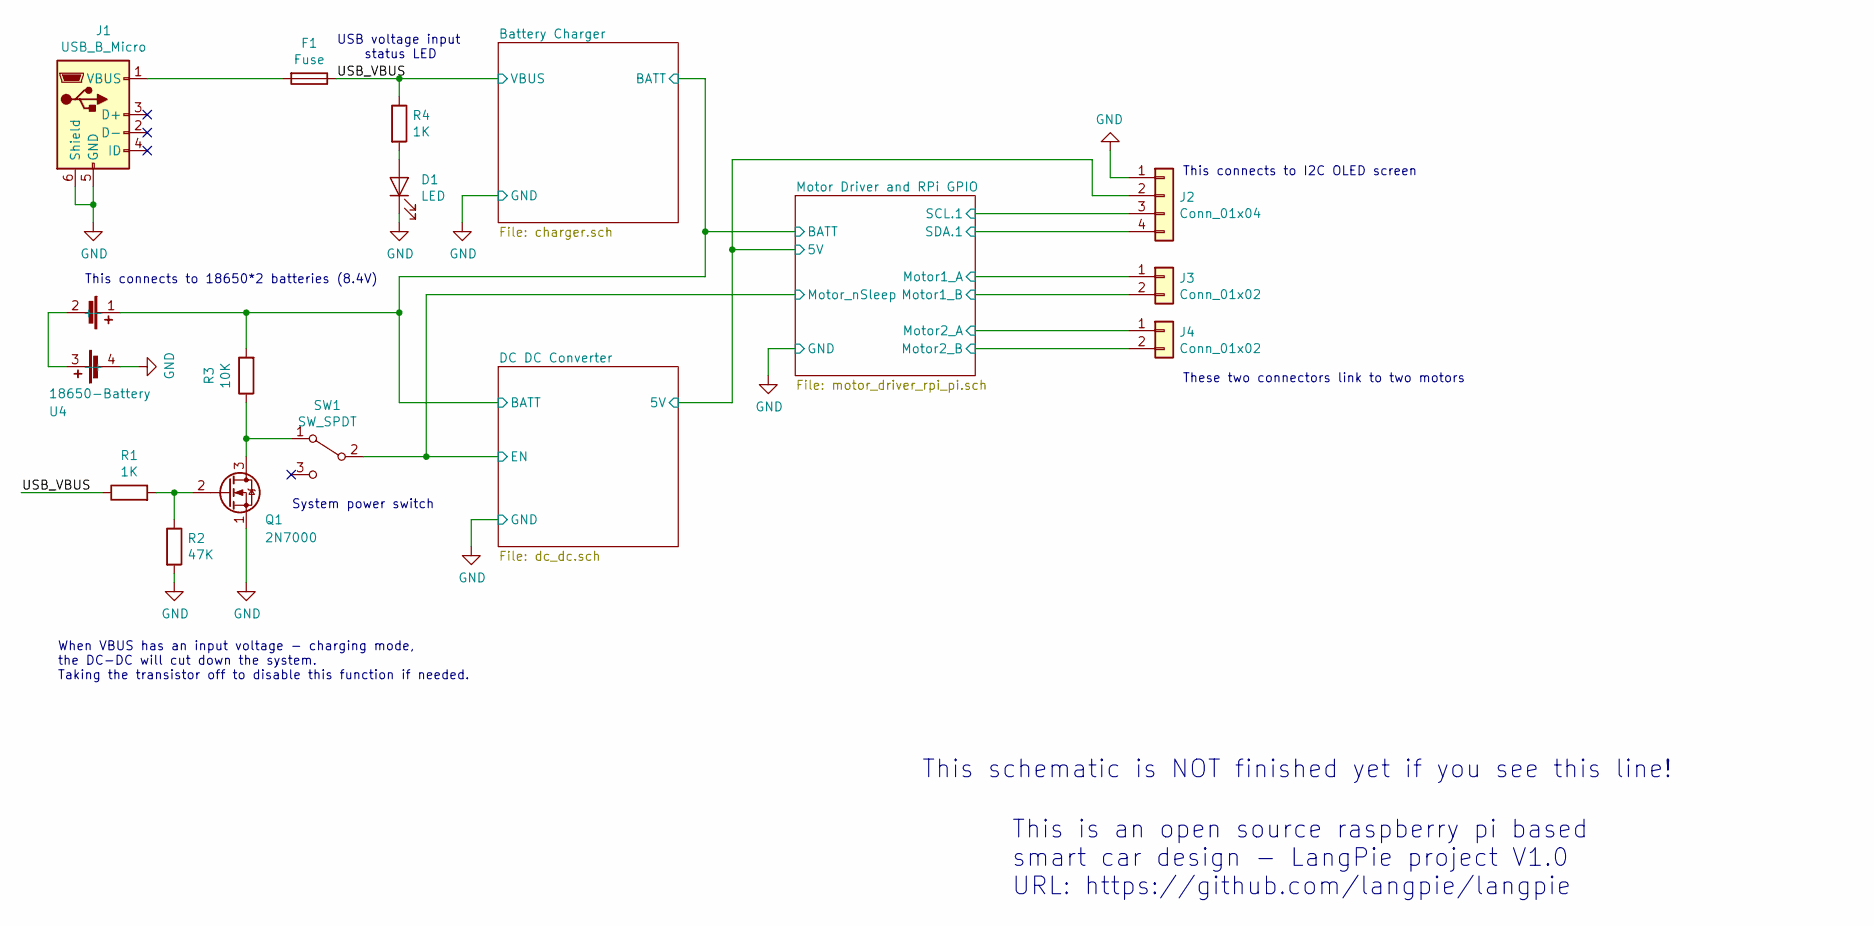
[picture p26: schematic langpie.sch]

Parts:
D1: LED; LED_0805_2012Metric
F1: Fuse; Fuse_1206_3216Metric
J1: USB_B_Micro; USB_Micro-B_GCT_USB3076-30-A
J2: Conn_01x04; PinHeader_1x04_P2.54mm_Vertical
J3, J4: Conn_01x02; SolderWirePad_1x02_P5.08mm_Drill1.5mm
Q1: 2N7000; SOT-23
R1, R4: 1K; R_0805_2012Metric
R2: 47K; R_0805_2012Metric
R3: 10K; R_0805_2012Metric
SW1: SW_SPDT; SW_CuK_OS102011MA1QN1_SPDT_Angled
U4: 18650-Battery; li-battery-case

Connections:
/Battery Charger/BATT: R3.2, U4.1 (+); also elsewhere on the board
/DC DC Converter/5V: J2.2; also elsewhere on the board
/DC DC Converter/EN: SW1.2 (B); also elsewhere on the board
/Motor Driver and RPi GPIO/Motor1_A: J3.1; also elsewhere on the board
/Motor Driver and RPi GPIO/Motor1_B: J3.2; also elsewhere on the board
/Motor Driver and RPi GPIO/Motor2_A: J4.1; also elsewhere on the board
/Motor Driver and RPi GPIO/Motor2_B: J4.2; also elsewhere on the board
/Motor Driver and RPi GPIO/SCL.1: J2.3; also elsewhere on the board
/Motor Driver and RPi GPIO/SDA.1: J2.4; also elsewhere on the board
/USB_VBUS: F1.1, R1.1, R4.1; also elsewhere on the board
GND: D1.1 (K), J1.5 (GND), J1.6 (Shield), J2.1, Q1.1 (S), R2.2, U4.4 (-); also elsewhere on the board
unnamed: D1.2 (A), R4.2
unnamed: F1.2, J1.1 (VBUS)
unnamed: Q1.2 (G), R1.2, R2.1
unnamed: Q1.3 (D), R3.1, SW1.1 (A)
unnamed: U4.2 (-), U4.3 (+)

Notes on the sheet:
When VBUS has an input voltage - charging mode, the DC-DC will cut down the system. Taking the transistor off to disable this function if needed.
USB voltage input status LED
This connects to I2C OLED screen
This connects to 18650*2 batteries (8.4V)
These two connectors link to two motors
System power switch
This is an open source raspberry pi based smart car design - LangPie project V1.0 URL: https://github.com/langpie/langpie
This schematic is NOT finished yet if you see this line!

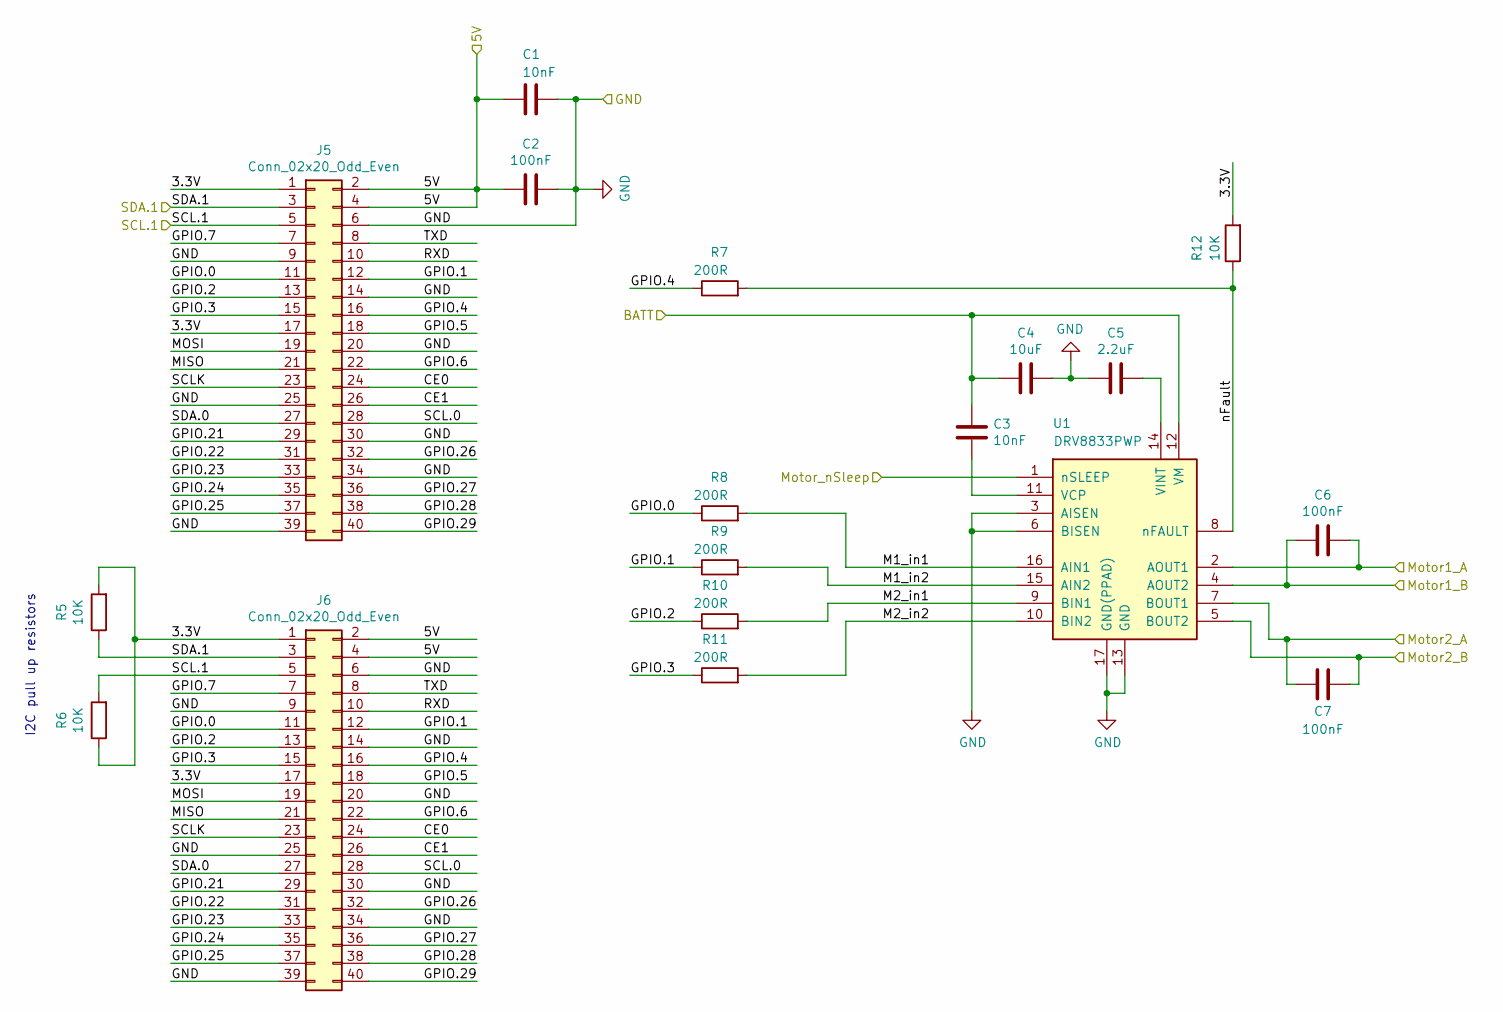
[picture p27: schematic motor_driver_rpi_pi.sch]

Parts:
C1: 10nF; C_1206_3216Metric
C2, C6, C7: 100nF; C_0805_2012Metric
C3: 10nF; C_0805_2012Metric
C4: 10uF; C_1206_3216Metric
C5: 2.2uF; C_0805_2012Metric
J5: Conn_02x20_Odd_Even; PinSocket_2x20_P2.54mm_Vertical
J6: Conn_02x20_Odd_Even; PinHeader_2x20_P2.54mm_Vertical
R5, R6, R12: 10K; R_0805_2012Metric
R7, R8, R9, R10, R11: 200R; R_0805_2012Metric
U1: DRV8833PWP; HTSSOP-16-1EP_4.4x5mm_P0.65mm_EP3.4x5mm_Mask2.46x2.31mm_The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

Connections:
/Battery Charger/BATT: C3.1, C4.2, U1.12 (VM); also elsewhere on the board
/DC DC Converter/5V: C1.2, C2.2, J5.2, J5.4, J6.2, J6.4; also elsewhere on the board
/DC DC Converter/EN: U1.1 (nSLEEP); also elsewhere on the board
/Motor Driver and RPi GPIO/3.3V: J5.1, J5.17, J6.1, J6.17, R5.2, R6.1, R12.2
/Motor Driver and RPi GPIO/CE0: J5.24, J6.24
/Motor Driver and RPi GPIO/CE1: J5.26, J6.26
/Motor Driver and RPi GPIO/GPIO.0: J5.11, J6.11, R8.1
/Motor Driver and RPi GPIO/GPIO.1: J5.12, J6.12, R9.1
/Motor Driver and RPi GPIO/GPIO.2: J5.13, J6.13, R10.1
/Motor Driver and RPi GPIO/GPIO.3: J5.15, J6.15, R11.1
/Motor Driver and RPi GPIO/GPIO.4: J5.16, J6.16, R7.1
/Motor Driver and RPi GPIO/GPIO.5: J5.18, J6.18
/Motor Driver and RPi GPIO/GPIO.6: J5.22, J6.22
/Motor Driver and RPi GPIO/GPIO.7: J5.7, J6.7
/Motor Driver and RPi GPIO/GPIO.21: J5.29, J6.29
/Motor Driver and RPi GPIO/GPIO.22: J5.31, J6.31
/Motor Driver and RPi GPIO/GPIO.23: J5.33, J6.33
/Motor Driver and RPi GPIO/GPIO.24: J5.35, J6.35
/Motor Driver and RPi GPIO/GPIO.25: J5.37, J6.37
/Motor Driver and RPi GPIO/GPIO.26: J5.32, J6.32
/Motor Driver and RPi GPIO/GPIO.27: J5.36, J6.36
/Motor Driver and RPi GPIO/GPIO.28: J5.38, J6.38
/Motor Driver and RPi GPIO/GPIO.29: J5.40, J6.40
/Motor Driver and RPi GPIO/M1_in1: R8.2, U1.16 (AIN1)
/Motor Driver and RPi GPIO/M1_in2: R9.2, U1.15 (AIN2)
/Motor Driver and RPi GPIO/M2_in1: R10.2, U1.9 (BIN1)
/Motor Driver and RPi GPIO/M2_in2: R11.2, U1.10 (BIN2)
/Motor Driver and RPi GPIO/MISO: J5.21, J6.21
/Motor Driver and RPi GPIO/MOSI: J5.19, J6.19
/Motor Driver and RPi GPIO/Motor1_A: C6.1, U1.2 (AOUT1); also elsewhere on the board
/Motor Driver and RPi GPIO/Motor1_B: C6.2, U1.4 (AOUT2); also elsewhere on the board
/Motor Driver and RPi GPIO/Motor2_A: C7.2, U1.7 (BOUT1); also elsewhere on the board
/Motor Driver and RPi GPIO/Motor2_B: C7.1, U1.5 (BOUT2); also elsewhere on the board
/Motor Driver and RPi GPIO/RXD: J5.10, J6.10
/Motor Driver and RPi GPIO/SCL.0: J5.28, J6.28
/Motor Driver and RPi GPIO/SCL.1: J5.5, J6.5, R6.2; also elsewhere on the board
/Motor Driver and RPi GPIO/SCLK: J5.23, J6.23
/Motor Driver and RPi GPIO/SDA.0: J5.27, J6.27
/Motor Driver and RPi GPIO/SDA.1: J5.3, J6.3, R5.1; also elsewhere on the board
/Motor Driver and RPi GPIO/TXD: J5.8, J6.8
/Motor Driver and RPi GPIO/nFault: R7.2, R12.1, U1.8 (nFAULT)
GND: C1.1, C2.1, C4.1, C5.2, J5.6, J5.9, J5.14, J5.20, J5.25, J5.30, J5.34, J5.39, J6.6, J6.9, J6.14, J6.20, J6.25, J6.30, J6.34, J6.39, U1.3 (AISEN), U1.6 (BISEN), U1.13 (GND), U1.17 (GND(PPAD)); also elsewhere on the board
unnamed: C3.2, U1.11 (VCP)
unnamed: C5.1, U1.14 (VINT)

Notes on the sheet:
I2C pull up resistors

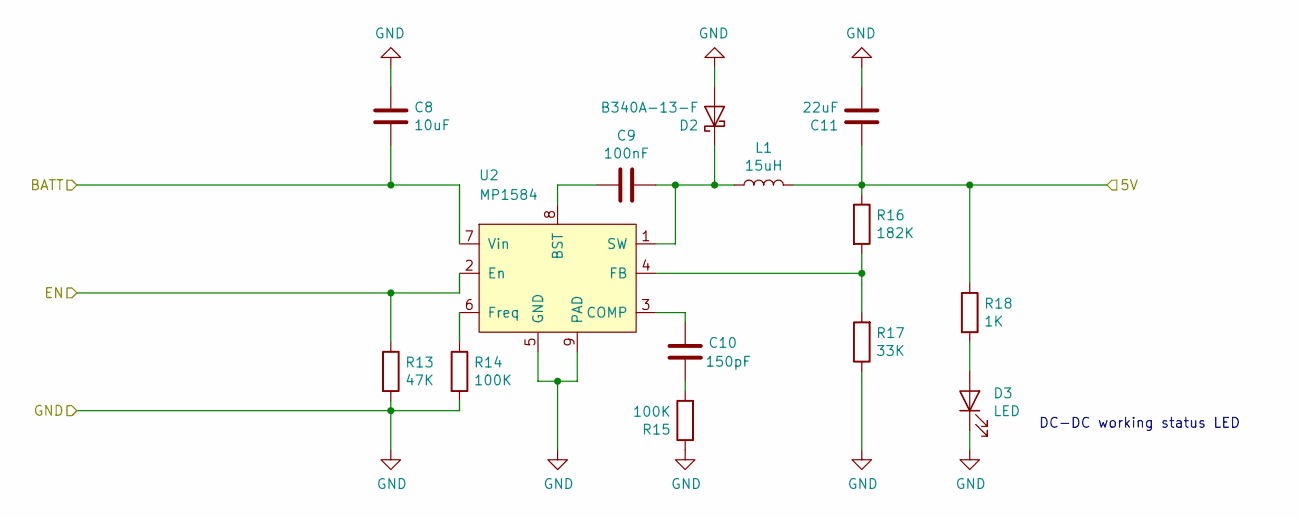
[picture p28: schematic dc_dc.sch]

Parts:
C8: 10uF; C_1206_3216Metric
C9: 100nF; C_0805_2012Metric
C10: 150pF; C_0805_2012Metric
C11: 22uF; C_1206_3216Metric
D2: B340A-13-F; D_SMA
D3: LED; LED_0805_2012Metric
L1: 15uH; L_12x12mm_H6mm
R13: 47K; R_0805_2012Metric
R14, R15: 100K; R_0805_2012Metric
R16: 182K; R_0805_2012Metric
R17: 33K; R_0805_2012Metric
R18: 1K; R_0805_2012Metric
U2: MP1584; SOIC-8-1EP_3.9x4.9mm_P1.27mm_EP2.29x3mm_ThermalVias

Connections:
/Battery Charger/BATT: C8.2, U2.7 (Vin); also elsewhere on the board
/DC DC Converter/5V: C11.1, L1.2, R16.1, R18.1; also elsewhere on the board
/DC DC Converter/EN: R13.1, U2.2 (En); also elsewhere on the board
GND: C8.1, C11.2, D2.2 (A), D3.1 (K), R13.2, R14.2, R15.1, R17.1, U2.5 (GND), U2.9 (PAD); also elsewhere on the board
unnamed: C9.1, D2.1 (K), L1.1, U2.1 (SW)
unnamed: C9.2, U2.8 (BST)
unnamed: C10.1, U2.3 (COMP)
unnamed: C10.2, R15.2
unnamed: D3.2 (A), R18.2
unnamed: R14.1, U2.6 (Freq)
unnamed: R16.2, R17.2, U2.4 (FB)

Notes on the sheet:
DC-DC working status LED

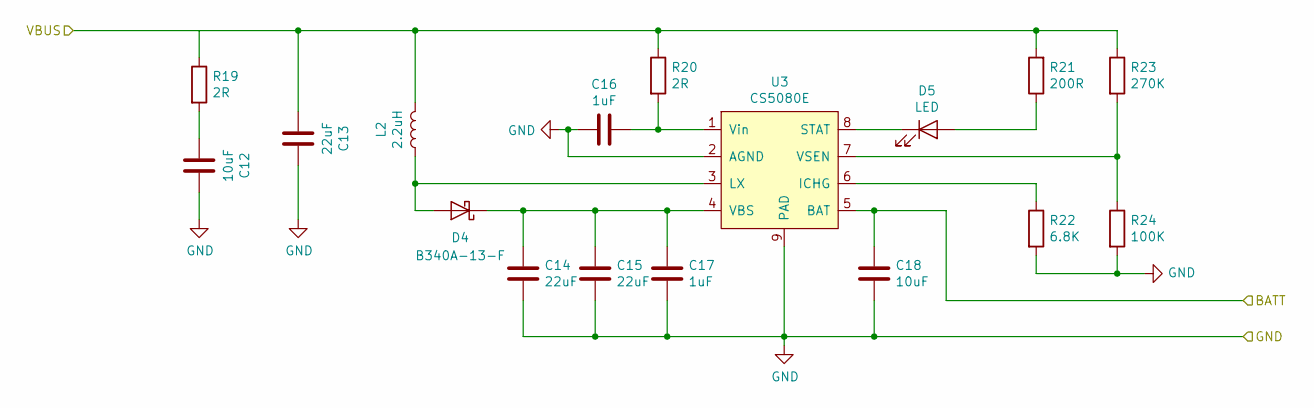
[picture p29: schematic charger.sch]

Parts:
C12, C18: 10uF; C_1206_3216Metric
C13, C14, C15: 22uF; C_1206_3216Metric
C16, C17: 1uF; C_0805_2012Metric
D4: B340A-13-F; D_SMA
D5: LED; LED_0805_2012Metric
L2: 2.2uH; L_12x12mm_H6mm
R19, R20: 2R; R_0805_2012Metric
R21: 200R; R_0805_2012Metric
R22: 6.8K; R_0805_2012Metric
R23: 270K; R_0805_2012Metric
R24: 100K; R_0805_2012Metric
U3: CS5080E; SOIC-8-1EP_3.9x4.9mm_P1.27mm_EP2.29x3mm_ThermalVias

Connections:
/Battery Charger/BATT: C18.1, U3.5 (BAT); also elsewhere on the board
/USB_VBUS: C13.2, L2.2, R19.1, R20.1, R21.2, R23.1; also elsewhere on the board
GND: C12.1, C13.1, C14.1, C15.1, C16.2, C17.1, C18.2, R22.2, R24.2, U3.2 (AGND), U3.9 (PAD); also elsewhere on the board
unnamed: C12.2, R19.2
unnamed: C14.2, C15.2, C17.2, D4.1 (K), U3.4 (VBS)
unnamed: C16.1, R20.2, U3.1 (Vin)
unnamed: D4.2 (A), L2.1, U3.3 (LX)
unnamed: D5.1 (K), U3.8 (STAT)
unnamed: D5.2 (A), R21.1
unnamed: R22.1, U3.6 (ICHG)
unnamed: R23.2, R24.1, U3.7 (VSEN)

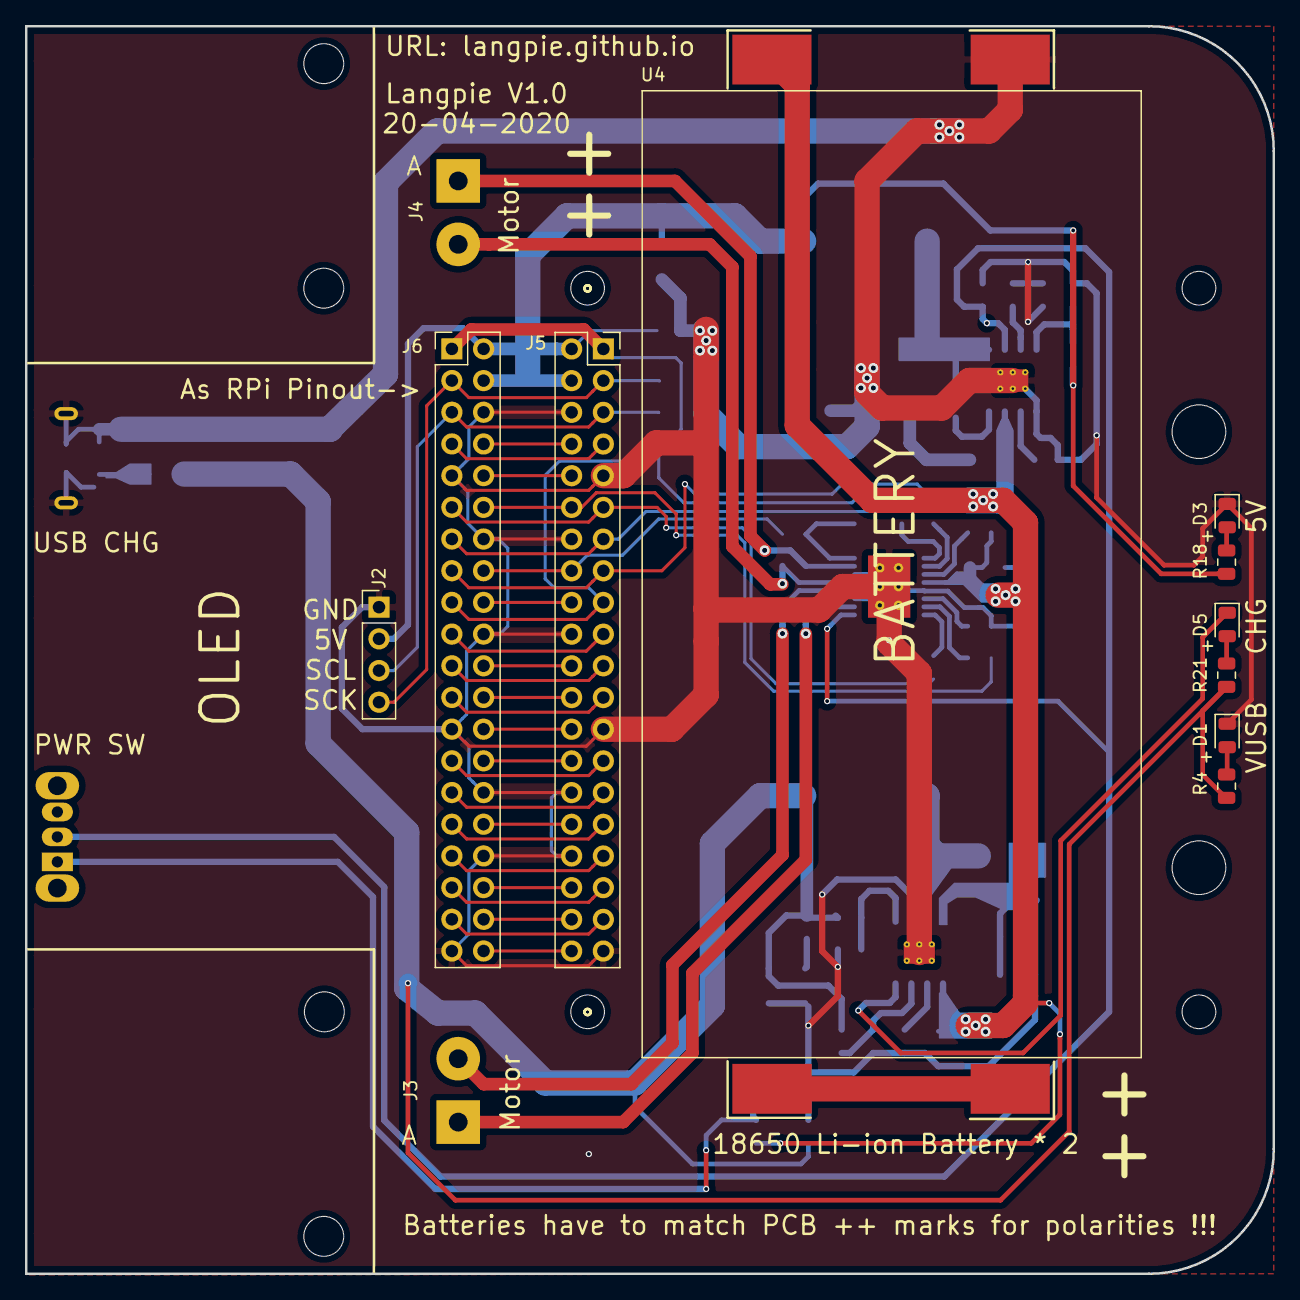
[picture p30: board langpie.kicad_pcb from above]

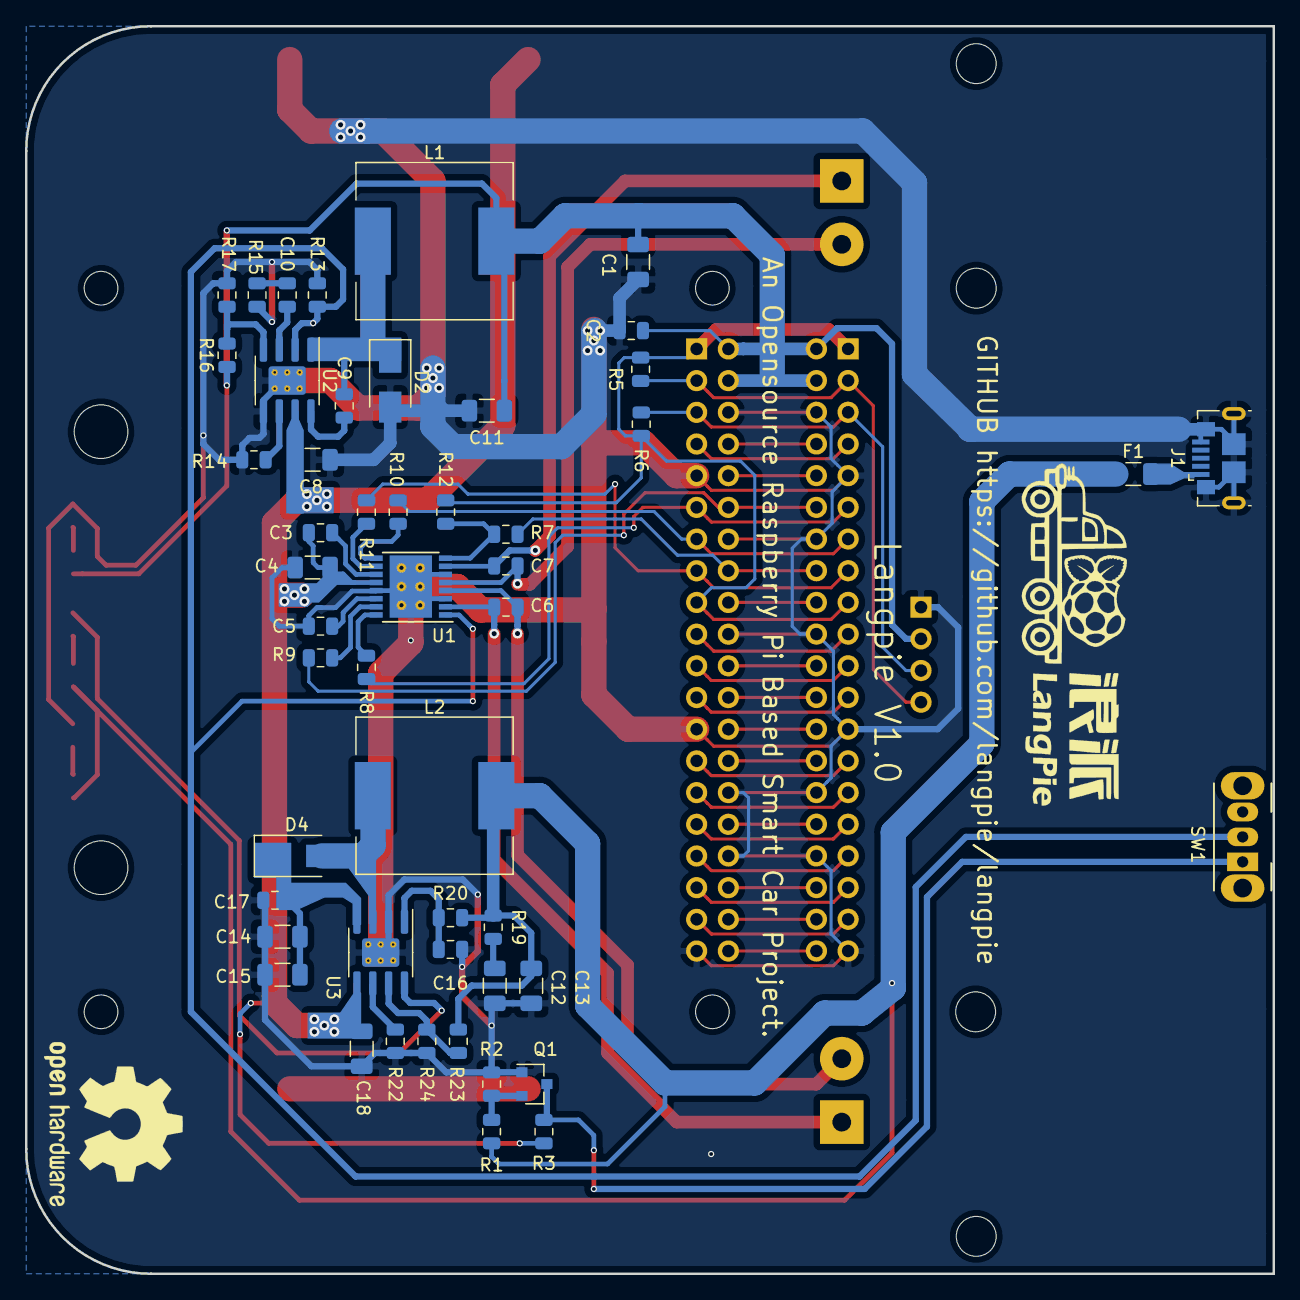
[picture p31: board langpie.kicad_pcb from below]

Board: 2 copper layers, 100.0 x 100.0 mm, 72 parts (50 on the bottom side), 65 nets.

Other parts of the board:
 : MountingHole_2.7mm_M2.5
 #2,  #3: MountingHole_4.3mm_M4
 #4,  #5,  #6: MountingHole_2.7mm_M2.5
 #7,  #8,  #9,  #10: MountingHole_3.2mm_M3

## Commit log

2020-04-07 Change one folder to 'mechanics', update electronics and pi 3d step file.
    [A12牛眼轮.SLDPRT, M2.5 20+6.SLDPRT, M2.5螺母.SLDPRT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]
2020-04-09 提交信息
    [M2.5 24+6.SLDPRT, M2.5 nut.SLDPRT, M3 8 hexagon socket head cap screw.SLDPRT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]
2020-04-10 优化了电机座增加了摄像头支架并创建了3D打印所需的STL文件
    [A12牛眼轮.SLDPRT, M2 8 hexagon socket head cap screw.SLDPRT, M2 nut.SLDPRT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]
2020-04-10 Change electronics design, update new SCHs...
    [charger.sch, dc_dc.sch, langpie.kicad_pcb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]
2020-04-10 update RPi GPIO SCH
    [charger.sch, dc_dc.sch, langpie.sch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]
2020-04-10 update Raspberry pi preparation file and update email list
2020-04-11 Slightly change electronics
    [charger.sch, dc_dc.sch]
2020-04-12 Update DCDC design, add a DCDC output calculator tool, add oled screen 3D models
    [dc_dc.sch, mp1584_dcdc_output_calculator.xlsx, oled_screen.STEP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]
2020-04-12 Change to electronics, and adding pi dimensions into documents
    [charger.sch, dc_dc.sch, langpie.sch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]
2020-04-12 Preview SCH is done, but not fully finished.
    [charger.sch, dc_dc.sch, langpie.sch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]
2020-04-12 A bug fix in electronics
    [langpie.sch]
2020-04-13 更新了V1.1版本的小车待完善
    [128x64Oled.step, 128x64Oled.step.SLDASM, M2 11+3 .SLDPRT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]
2020-04-13 基本完善了V1.1版本的小车
    [128x64Oled v3.sldprt, 128x64Oled(2).sldasm, 128x64Oled.SLDASM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]
2020-04-14 改进了V1.1版本的小车
    [M2 6 hexagon socket head cap screw.SLDPRT, M2 8 hexagon socket head cap screw.SLDPRT, M2.5 24+6.SLDPRT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]
2020-04-14 Electronics define IOs to motor driver.
    [langpie.sch, motor_driver_rpi_pi.sch]
2020-04-14 modified: ../../electronics/charger.sch modified: ../../electronics/charger.sch-bak modified: ../../electronics/dc_dc.sch modified: ../../electronics/dc_dc.sch-bak modified: ../../electronics/langpie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
    [charger.sch, dc_dc.sch, langpie.sch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]
2020-04-15 update pcb file and netlist
    [langpie.sch, motor_driver_rpi_pi.sch, rpi_MECH_3bplus.dxf]
2020-04-18 Adding PCB and PCB library
    [langpie.kicad_pcb, langpie.sch]
2020-04-18 Finish PCB, silightly change to SCH, Gerber generated, V1.0 HW almost done.
    [charger.sch, dc_dc.sch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]
2020-04-19 Finalise the design and send to manufactory already for the V1
    [langpie.csv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]
2020-04-25 Adding real PCB look pictures.
2020-09-10 add 1.54inch e-paper for langpie with schematic
    [epd1.54inch.kicad_pcb, epd1.54inch.sch]
